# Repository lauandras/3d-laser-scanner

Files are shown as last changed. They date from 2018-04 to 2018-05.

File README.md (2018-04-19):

# 3d-laser-scanner
This is our 3D-laser scanner project from Mechatronics project subject.

Downloaded MatLab packages:
  1) MATLAB Support Package for Arduino Hardware
  2) MATLAB Support Package for USB Webcams
  3) Computer Vision System Toolbox
  4) a
  5) a

Exercise - Feladat (HU)
1 mm alatti felbontással bíró lézer szkenner tervezése, amely alkalmas legalább 300x300x500 mm-es tárgyak külső felületének letapogatására.
Szakirodalom kutatás: Tekintsék át a 3D-s szkennelési eljárásokat, különös tekintettel a Lézeres letapogatásra.
Fejlesztés: Végezzék el a lézeres 3D-s szkenner tervezését és kivitelezését, két webkamera és egy vonallézer felhasználásával. A szerkezet legyen alkalmas a szerkezet együttes szállítására, tárolására és szabványos fényképezőállványra való rögzítésre. 
Tervezzenek (a másik 3D szkenneres csoporttal együttműködve) forgatóasztalt kisméretű (max. 500x500x500 mm) tárgyak 360°-os letapogatásához, amely alkalmas a kamerákkal való szinkronizált mozgatásra.

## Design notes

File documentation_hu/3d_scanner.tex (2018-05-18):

\documentclass[12pt,a4paper]{article}
\usepackage[utf8]{inputenc}
\usepackage{pdfpages}
\usepackage[magyar]{babel}
\usepackage{hyperref}	
\hypersetup{					
colorlinks=false,						
pdfborder={0 0 0},
}
\usepackage{fancyhdr}
\usepackage[left=2cm,right=2cm,top=3.5cm,bottom=3cm,headsep=50pt]{geometry}

%=================================================
% code snippset settings
%=================================================
\usepackage{listings}
\usepackage{color}

\usepackage[framed,numbered]{matlab-prettifier}

\definecolor{dkgreen}{rgb}{0,0.6,0}
\definecolor{gray}{rgb}{0.5,0.5,0.5}
\definecolor{mauve}{rgb}{0.58,0,0.82}
\definecolor{mygreen}{RGB}{28,172,0} % color values Red, Green, Blue
\definecolor{mylilas}{RGB}{170,55,241}

\lstset{language=Matlab,%
	%basicstyle=\color{red},
	breaklines=true,%
	morekeywords={matlab2tikz},
	keywordstyle=\color{blue},%
	morekeywords=[2]{1}, keywordstyle=[2]{\color{black}},
	identifierstyle=\color{black},%
	stringstyle=\color{mylilas},
	commentstyle=\color{mygreen},%
	showstringspaces=false,%without this there will be a symbol in the places where there is a space
	numbers=left,%
	numberstyle={\tiny \color{black}},% size of the numbers
	numbersep=9pt, % this defines how far the numbers are from the text
	emph=[1]{for,end,break},emphstyle=[1]\color{red}, %some words to emphasise
	%emph=[2]{word1,word2}, emphstyle=[2]{style},    
}

\begin{document}
%=================================================
\thispagestyle{empty}
\begin{center}
\\
\large{Budapesti Műszaki- és Gazdaságtudományi Egyetem\\
Gépészmérnöki kar}\\[1cm]
\begin{Huge}
\textbf{Mechatronika projekt}
\end{Huge}\\[0.5cm]

\Large{BMEGEFOAMM3}\\[2cm]
\Huge{\bf{3D szkenner}}\\[2.5cm]
\bf{\Large{Tar Dániel\\[5pt]
		Bognár Máté\\
		Varga Roland}}\\[1cm]

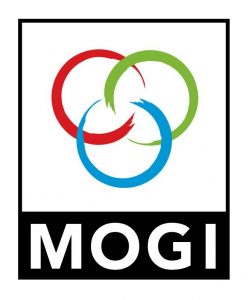
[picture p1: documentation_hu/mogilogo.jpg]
\\[1cm]
\large{\today}
\end{center}
%=================================================
\newpage
\tableofcontents
\newpage
\pagestyle{fancy}
\fancyhf{}
\rhead{Tar Dániel\\Bognár Máté\\Varga Roland}
\lhead{3D szkenner}
\cfoot{\thepage. oldal}
%=================================================
\section{Bevezető} %vargar
Az iparban egyre elterjedtebb a 3D szkennerek alkalmazása. Jól használhatóak gyors prototípuskészítésre és `'reverse engineering'' eljárásokhoz. Ezzel jelentős modellezési és mérési idő takarítható meg.\\[10pt]
Új eszközök tervezésénél és komplex alkatrészek méreteinek gyors meghatározására egyaránt használható. Apróbb mechanikai alkatrészek, turbinalapátok és helységek szkennelése is lehetséges adott felbontással.\\[10pt]
A gyógyászatban alkalmazzák például test vagy testrész modellezésére, mivel egyes protézisek elkészítése nagy méretpontosságot igényel, és így könnyebben formálhatóak az egyéni igények szerint.\\[10pt]
Egyetemeken régészek is használhatják leletek tanulmányozására anélkül, hogy bármilyen kártétel veszélye fennállna.\\[10pt]
\begin{figure}[h!]
\centering
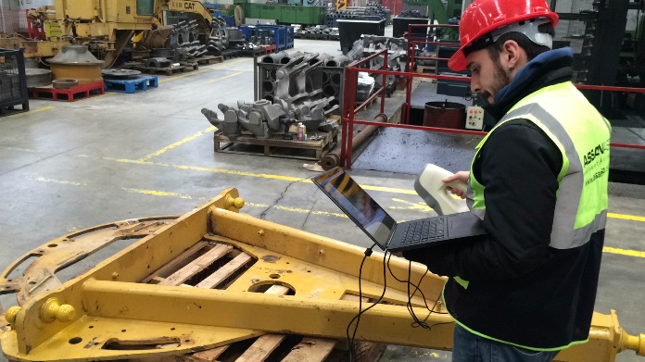
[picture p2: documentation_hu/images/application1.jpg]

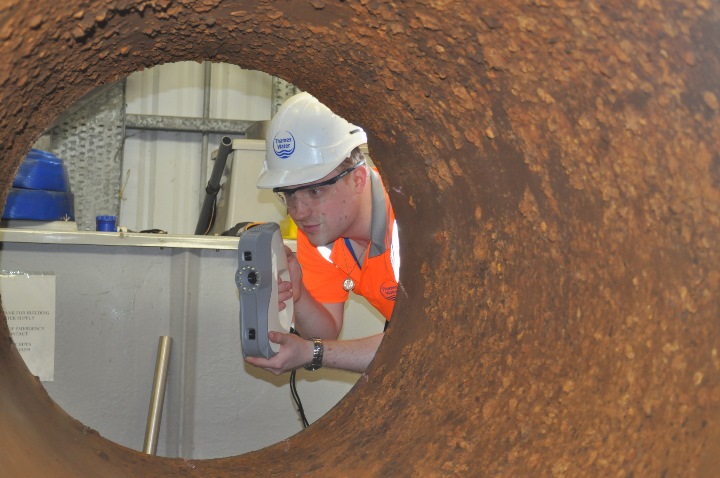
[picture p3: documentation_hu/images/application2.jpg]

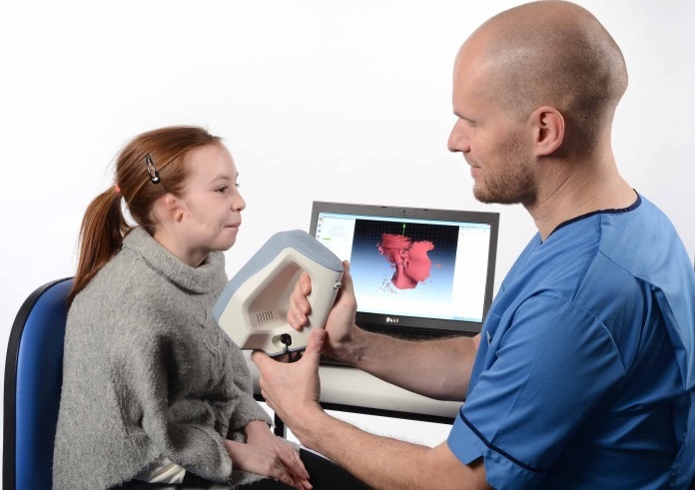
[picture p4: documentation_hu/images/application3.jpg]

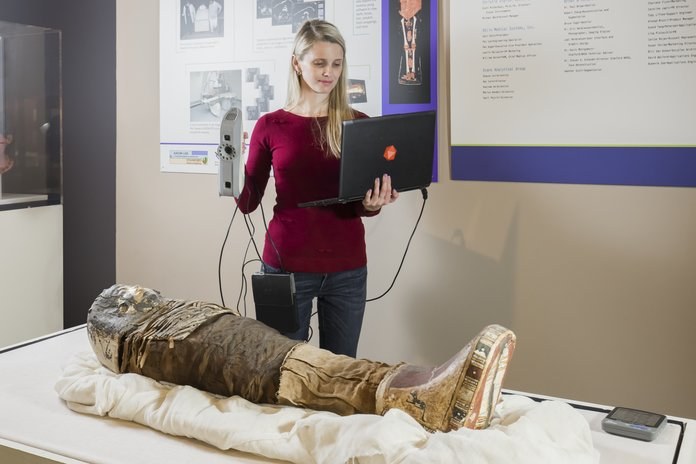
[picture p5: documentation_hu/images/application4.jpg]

\caption{3D szkenner alkalmazása a hétköznapokban\cite{alkalmazasok}}
\end{figure}
%=================================================
\newpage
\section{Feladat leírása} %vargar
\subsection{Követelmények}
A projekt célja egy használható 3D lézerszkenner eljárás kidolgozása és megvalósítása, ami az alábbi követelményeknek megfelel:
\begin{enumerate}
	\item A konstrukció hordozhatósága: viszonylag kis befoglaló mérettel kell 			rendelkezzen és könnyen szétszerelhető-összerakható legyen.\label{hordozhatosag}
	\item A szerkezet legyen alkalmas a szerkezet együttes szabványos fényképezőállványra való rögzítésére.\label{kameraallvanyra}
	\item A megírt program átláthatóságára (felhasználóbarát) és jól dokumentáltságára kell törekedni, hogy a projektet a későbbiekben mások is tovább tudják vinni.\label{felhasznalobarat}
\end{enumerate}
\subsection{Alap koncepció}
A szkennelési módszert egy webkamera, egy vonallézer és egy forgóasztal felhasználásával dolgoztuk ki. Az eljárás lényege, hogy a tárgyra vetült lézerfény vonalról a kamerával valamekkora szögből kép készül. A képen a forgóasztal forgástengelyének meghatározhatónak kell lennie, és ez a vonallézer által meghatározott síkba kell hogy essen. A lézerpontok forgástengelytől (és azon egy tetszőleges origótól) vett távolságából a térbeli helyzetük meghatározható.
%=================================================
\section{Alapul vett szakirodalom} % tard
%=================================================
	%"3d laserscanner" kulcsszót beírva a Google-be rengeteg találatot kap az ember. Mi elsőnek a képi és videó találatokat %nézegettük meg, és rögtön megállapítottuk, hogy nagyon menő lesz az általunk készített kis kütyü / szerkezet.\\
	
	Alapvetően kétféle lézer szkenner található meg a piacon. Az egyik, ami az adott tárgyat, objektumot végigpásztázza egy lézerfény segítségével és a lézerfény kibocsájtásától, a lézerfény visszaérkezéséig eltelt időből számítja a távolságot. Ez egy elég drága technika, mert nagyon pontosan kell mérni az időt. Mivel a fény terjedési sebessége nagyon nagy, ezért körülbelül $[ns]$ nagyságrendben kell mérni az idő múlását.\\[10pt]
	\begin{figure}[h!]
		\begin{center}
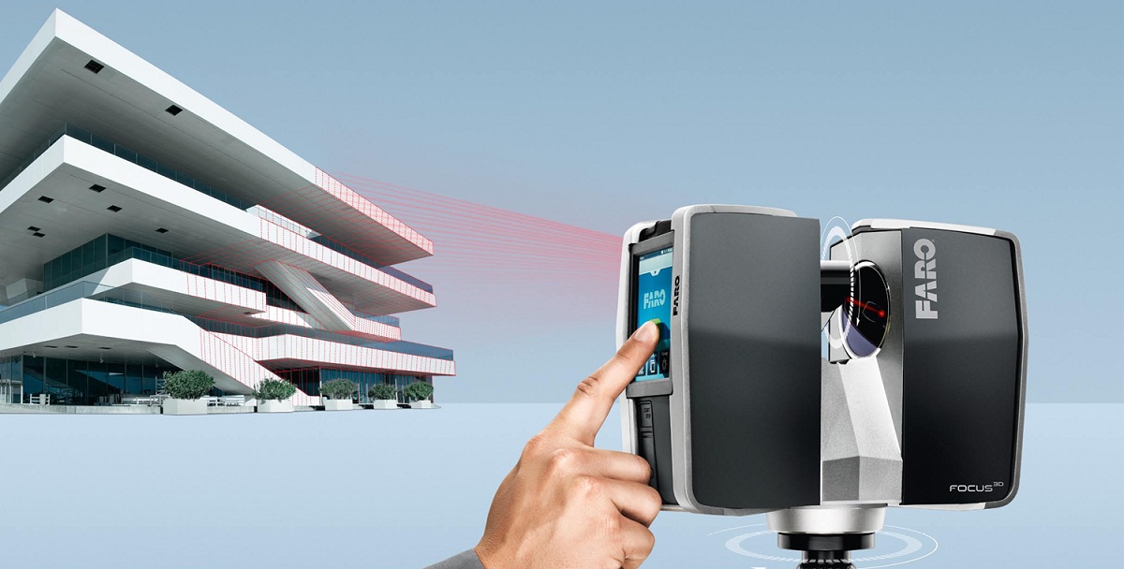
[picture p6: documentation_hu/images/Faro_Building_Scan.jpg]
			
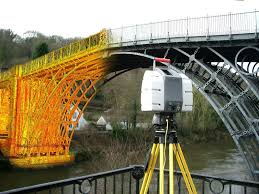
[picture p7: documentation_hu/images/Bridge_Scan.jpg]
			
		\end{center}
		\caption{Távolságmérésen alapuló lézerszkenner\cite{FaroBuildingScan}\cite{BridgeScan}}
	\end{figure}
	A másik, ami egy vonallézerrel világítja meg a tárgy felületét, majd képfeldolgozással felismerve a megvilágított élt, különböző módszerek alapján, előállít egy pontfelhőt. A pontfelhőből háromszögeléses technikával pedig elkészít egy felületmodellt.\\[10pt]
	\begin{figure}[h!]
		\begin{center}
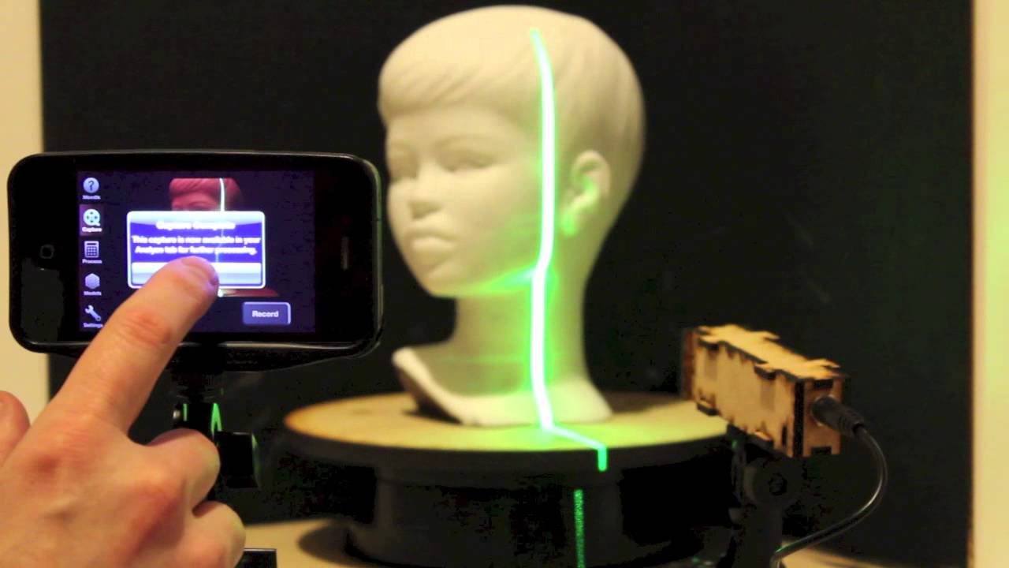
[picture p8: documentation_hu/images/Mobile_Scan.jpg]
			
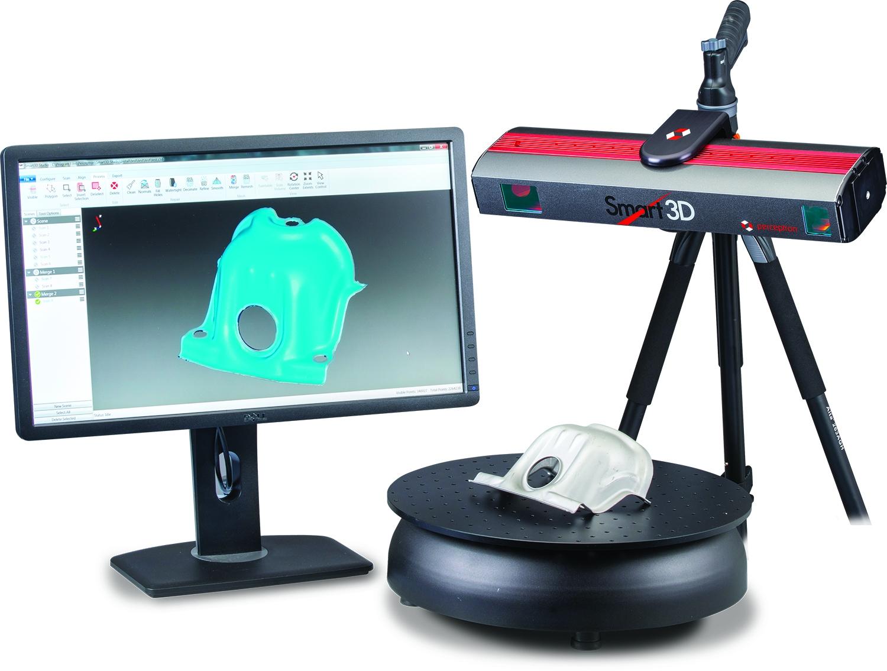
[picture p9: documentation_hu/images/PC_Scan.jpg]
			
		\end{center}
		\caption{Forgóasztalos, képfeldolgozáson alapuló\cite{MobileScan}\cite{PCScan}}
	\end{figure}\\[10pt]
	A rendelkezésre álló eszközök, a feladatleírás és a költségek alapján a második módszert választottuk. A projekt kiindulása képen nagy segítségünkre volt az \href{http://www.instructables.com/id/3D-Laser-Scanning-DIY/}{\textit{Instructables}} oldalon található \textit{DIY: How to Make a Low Cost 3D Scanner}\cite{LaserScannerProjekt} nevű projekt. Ez adott alapot a gondolkodásmódunknak, de végül teljesen más módszerrel dolgozzuk fel az adatokat.

%=================================================
\section{Felhasznált hardverek} % bognarm
%=================================================
\subsection{Beszerzett eszközök}
A projektfeladat már az előző évben is ki volt adva, a tavalyi csoportnak ugyan nem sikerült befejeznie, de néhány általuk készített alkatrész öröklődött. Így már kézhez kaptuk egy  LFL650-5-12(9x20)60-as típusú vonallézert,
egy unipoláris léptető motort, a tanszéki KUTESZ alkatrészekből összeállított állvánnyal és egy kisebb méretű asztallal,
illetve a motor meghajtó áramkört is.
\\[10pt]
A felhasznált hardverek egy másik része Bojtos Attila tanár úrtól származik. Ilyen a fényképezőgép állvány, az erre később rögzített 20x20-as ITEM-5-ös profil, és egy Canyon márkájú, 640x480-as felbontású webkamera.
\\[10pt]
Általunk beszerzett alkatrészek még a következőek: 
\begin{itemize}
	\item 2 db Arduino Nano v3
	\item HC-06 Bluetooh-Serial modul
\end{itemize}
 \begin{figure}[h!]
 	\centering
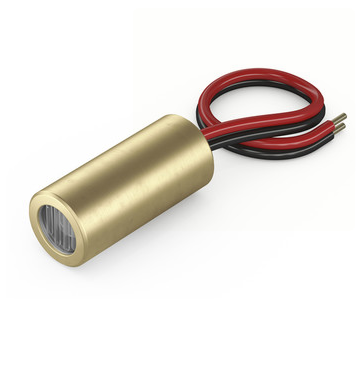
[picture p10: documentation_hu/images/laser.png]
 	
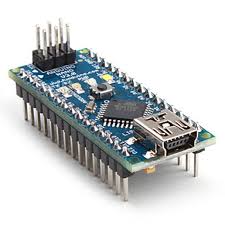
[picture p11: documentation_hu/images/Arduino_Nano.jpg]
 	
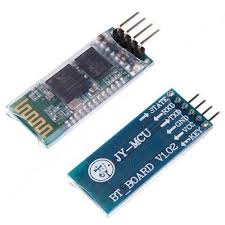
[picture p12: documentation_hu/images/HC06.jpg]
	
	\caption{Beszerzett eszközök}
\end{figure}

\subsection{Saját készítésű eszközök}
Az általunk tervezett alkatrészek többsége 3D nyomtatással készült, ezek a kamerát és lézert az ITEM profilra rögzítő elemek. A lézer lefogó, amely a lézert rögzíti a profil közepén. És a kamera tartó, ami két alkatrész közé szorítja be a kamera alsó részét, a gyári foglalathoz hasonló módon.\\[10pt]
Emellett a követelményeknek megfelelő szkennelhető tárgyméret miatt tervezni kellett egy új forgóasztalt. Ez az asztal 180mm átmérőjű, központosító körökkel ellátott, a KUTESZ elemekkel kompatibilis furatkiosztású elem.
Végül a profilt a kamera állványra rögzítő elem egy 6mm vastag,  lemez alkatrész.
 \begin{figure}[h!]
 	\centering
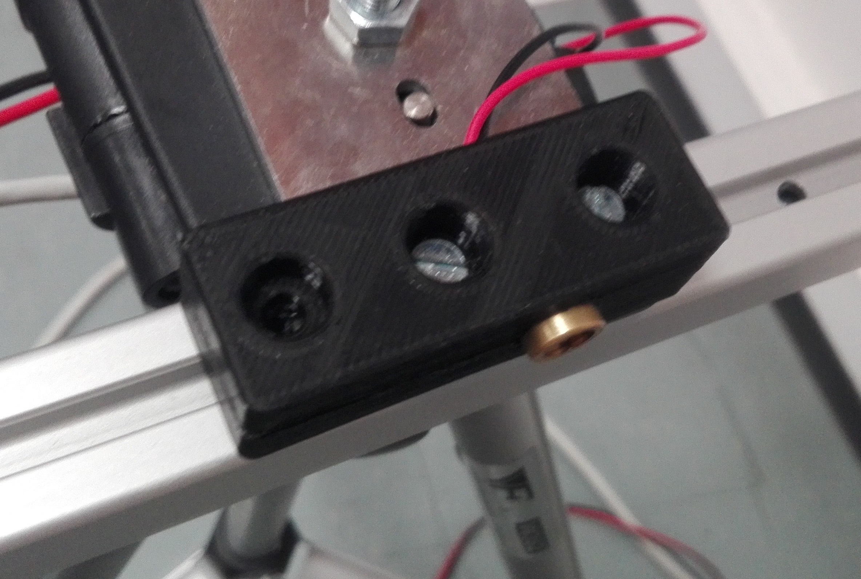
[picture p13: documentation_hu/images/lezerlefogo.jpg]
	
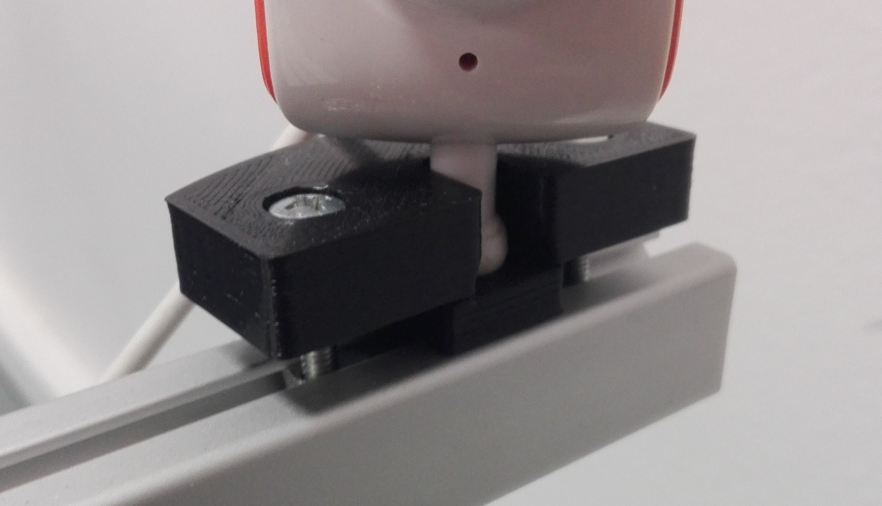
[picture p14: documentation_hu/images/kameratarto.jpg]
	
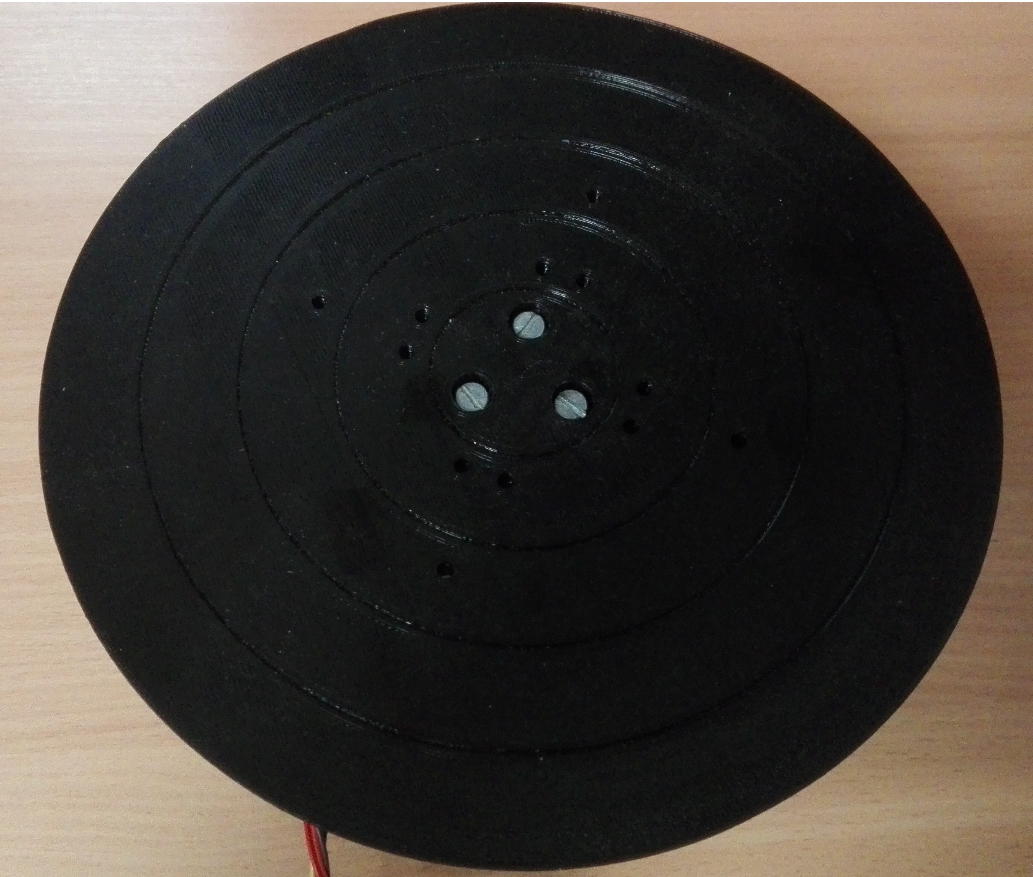
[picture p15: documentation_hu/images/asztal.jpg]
	
	\caption{Saját készítésű eszközök}
\end{figure}\\[10pt]
Készítettünk továbbá még két áramkört, amivel képesek vagyunk Bluetooth-on keresztül vezérelni a forgóasztalt, illetve egy vonallézer vezérlőt, amivel ki-be tudjuk kapcsolgatni a lézert szoftveresen. 

 \begin{figure}[h!]
	\centering
	
	
	\caption{Saját készítésű eszközök}
\end{figure}

\subsection{Hardverek közötti csatlakozás}

Az elkészült konstrukció két részből áll. Az egyik a forgóasztal, a motor, a meghajtója és ennek vezérlő áramköre. A meghajtónak hálózati tápellátás szükséges, míg a vezérlő jelenleg számítógépről kapja az áramot USB-n keresztül.
\\[10pt]
A másik rész a kamera állvány, rajta a lézerrel és webkamerával. Utóbbi közvetlen csatlakozik a számítógéphez, míg a lézer az őt vezérlő arduino-n keresztül, szintén USB segítségével. [\ref{kameraallvanyra}]
\\[10pt]
Így a szkenner két részben hordozható kivitelű. [\ref{hordozhatosag}]
 \begin{figure}[h!]
	\centering
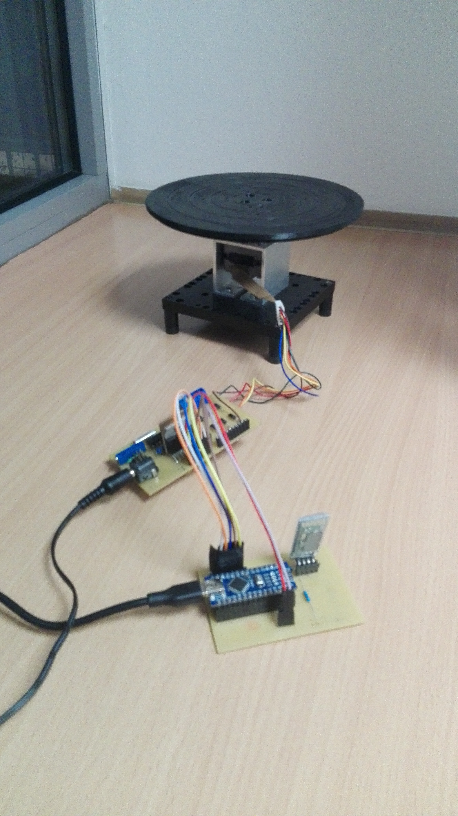
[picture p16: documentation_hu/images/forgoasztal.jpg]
	
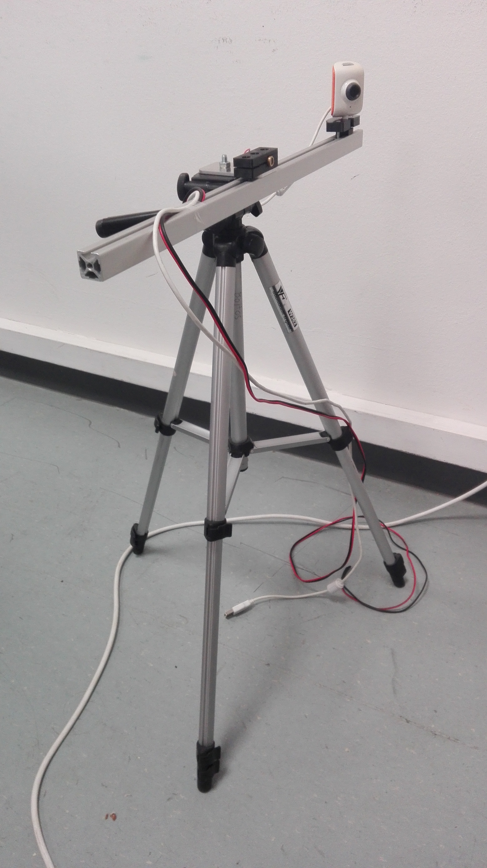
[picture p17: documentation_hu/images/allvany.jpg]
	
	\caption{Saját készítésű eszközök}
\end{figure}
%=================================================
\section{Programkód} %tard
%=================================================
Az egyes szorosan összetartozó részeket külön függvényben írtuk meg, amiket a főprogram, a scan\_object.m hív meg. A függvények csak a továbbiakban is használt változókat adják vissza, így redukáltuk a Workspace-en található vektorok számát. A továbbiakban ezeket fogjuk részletezni elmagyarázni.
%=================================================
\subsection{Kamera kalibráció}
A kamera kalibrációt elsőnek a lézert vezérlő Arduino csatlakoztatásával kezdjük, majd bekapcsoljuk a vonallézert. Ez azért szükséges, hogy a forgóasztal forgástengelyét pontosan a lézer vonalába lehessen helyezni.\\[10pt]
Következő lépésben ellenőrizzük, hogy nincs-e már kalibrálva. Ha igen, akkor ugrunk a következő szekcióra, ha nem akkor pedig megkezdjük a kalibrációs lépéseket:
\begin{enumerate}
	\item Camera Calibrator megnyílása
	\item Képek hozzáadása
	\begin{figure}[h!]
		\centering
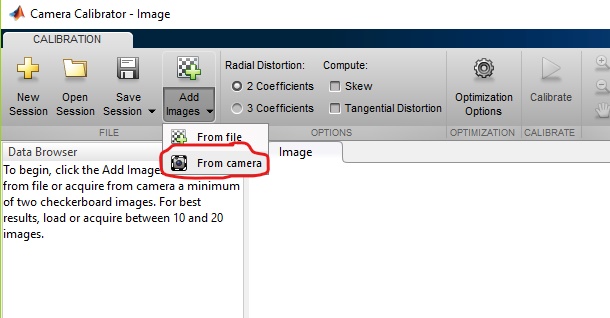
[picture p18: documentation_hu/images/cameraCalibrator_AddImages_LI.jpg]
		
		\caption{Camera Calibrator-ban a képek hozzáadása}
	\end{figure}
	\item A Camera fülön a kameránk kiválasztása
	\item Képek mentési helyének kiválasztása
	\item A képkészítések idejének beállítása
	\item A készítendő képek számának megadása
	\begin{figure}[h!]
		\centering
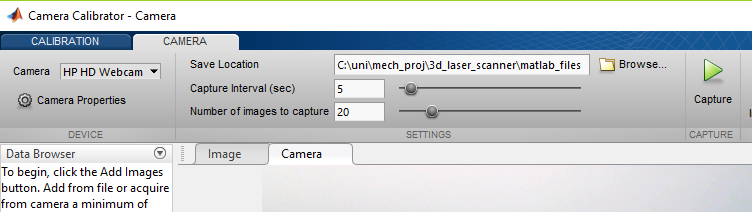
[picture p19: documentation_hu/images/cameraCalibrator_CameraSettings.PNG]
		
		\caption{Képkészítési beállítások megadása}
	\end{figure}
	\item Ha mindent jól beállítottunk, a Capture gombra kattintás 
\end{enumerate}
A sakktáblát célszerű különböző távolságokra, különböző szögekben tartani a kamerához képest, mert akkor pontosabban tud dolgozni az algoritmus. Ajánlott legalább 10-15 kép elkészítése, mielőtt eljutnánk a kalibrációnk kritikus, legnagyobb precizitást igénylő pontjához, a forgástengely beállításához.\\[10pt]
Most úgy kell még 3 képet készíteni, hogy a sakktábla egyik határolóvonala a forgástengellyel egybe essen, merőleges legyen a forgóasztalra és párhuzamos legyen a vonallézernyalábbal. Attól függően, hogy ezt a lépést milyen pontosan végezzük el, befolyásoljuk a beszkennelt 3d-modellünk pontosságát.\\[10pt]
A képek elkészülése utáni felugró ablakban meg kell adni a sakktáblánk egy elemének a méreteit.\\[10pt]
\begin{figure}[h!]
	\centering
	
	\caption{Sakktábla rácsméretének a megadása}
\end{figure}\\[10pt]
A \textit{Calibration} fülön az \textit{Optimization Options}-re, a \textit{Calibrate}, majd az \textit{Export Camera Parameters}-re kattintva ebben a sorrendben, már csak egy lépés marad a kalibrációs folyamatból: Matlab \textit{Command Window}-jában megadni annak a képnek a számát, amelyiken a sakktáblánk párhuzamos volt a lézernyalábbal. A kalibráció során a \textit{Matlab} algoritmusa meghatározza a mintán a négyzetek sarokpontjait, amikhez később, a 5.4-es pontban szükségünk lesz a képtranszformáció meghatározásában.

\begin{figure}[h!]
	\centering
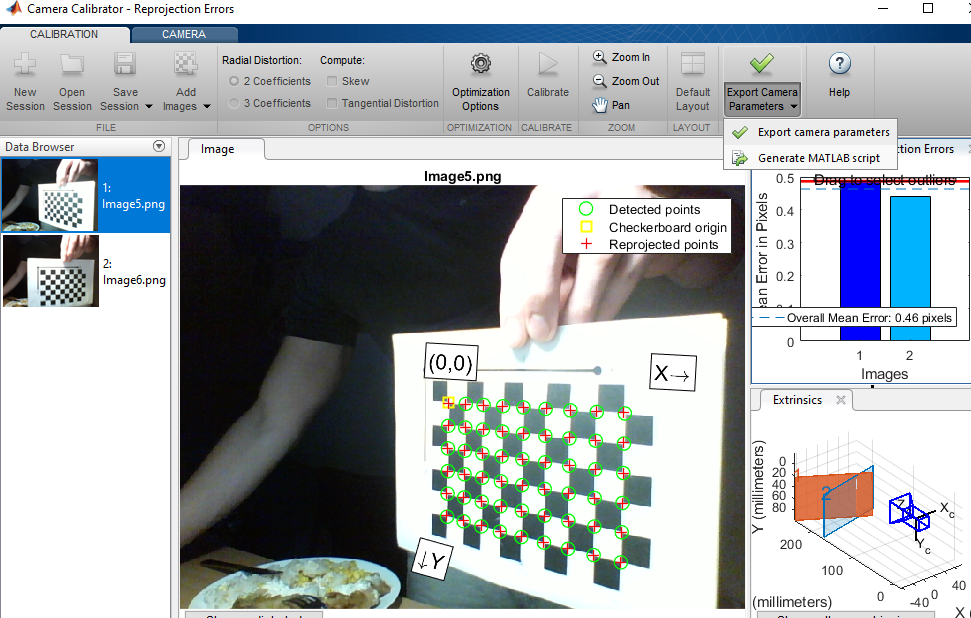
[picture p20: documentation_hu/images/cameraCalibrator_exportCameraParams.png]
	
	\caption{A kalibráció utólsó lépései}
\end{figure}

\begin{figure}[h!]
\centering
\begin{lstlisting}[
style = Matlab-editor,
basicstyle=\tiny
]
%----------------------------------------------------
%   Camera calibration
%----------------------------------------------------

% laserPin - the pin, on which the linelaser is soldered to
laserPin = 'D2';
prompt = 'On which Port is the laser controlling Arduino is connected: ';
laserCom = input(prompt,'s');

% connecting to the laser controlling Arduino on Port 'laserCom'
laserDino = arduino(laserCom,'Nano3');
disp('Laser connected')

% switch on the laser, that you can place the table so, that the laserline
% intersect the rotation axis
writeDigitalPin(laserDino,laserPin,1);

% if 'cameraParams' variable exists, then the calibration process is already done 
if (exist('cameraParams','var')~=1)
% if not then clear the variables for webCam - 'cam', the camera
% calibration toolbox will use it
clear cam

disp('Make minimum 15 pictures, then more 3 so,'+... 
+'that the chessboard pattern is parallel with the laserline!')

% starting camera calibration toolbox
cameraCalibrator
prompt = 'What is the number of the picture, on '+...
+'what the laserline is parallel with the chessboard: ';
paralellImageNumber = input(prompt);
end
\end{lstlisting}
\caption{Kamera kalibrációs rész kódja a scan\_object.m szkriptből}
\end{figure}

%=================================================
\subsection{Perifériák inicializálása}
Ellenőrizzük, hogy az adott perifériák léteznek-e a 'workspace'-n, ha bármelyik hiányzik, akkor kitöröljük mindet, majd újrainicializálunk az \textit{init()} függvény segítségével.
\begin{figure}[h!]
\centering
\begin{lstlisting}[
style = Matlab-editor,
basicstyle=\tiny
]
%----------------------------------------------------
%   Initialization
%----------------------------------------------------

% if there are no camera or laser or turntable variables
% on the workspace

% exist name -- returns 1 if 'name' is a variable in the workspace and 0 if
% not
if ((exist('a','var')&&exist('laserDino','var')&&exist('cam','var'))~=1)
clear a
clear cam
clear laserDino
[a,laserDino,cam]=init(laserCom);
end
\end{lstlisting}
\caption{Az eszközök inicializáló kódja a scan\_object.m szkriptből}
\end{figure}
	
\begin{figure}
\centering
\lstinputlisting[
style = Matlab-editor,
basicstyle=\tiny
]{../matlab_files/init.m}
\caption{Az init() függvény}
\end{figure}

%=================================================
\subsection{Képek vágása}
A szkennelt test felületén lévő piros lézercsík felismerésének, illetve az összes számolás gyorsításához a felhasználó kijelölheti a tárgyat befoglaló területét, majd egy jobb klikkes menüből levághatja a felesleges részeket.
\begin{figure}[h!]
	\centering
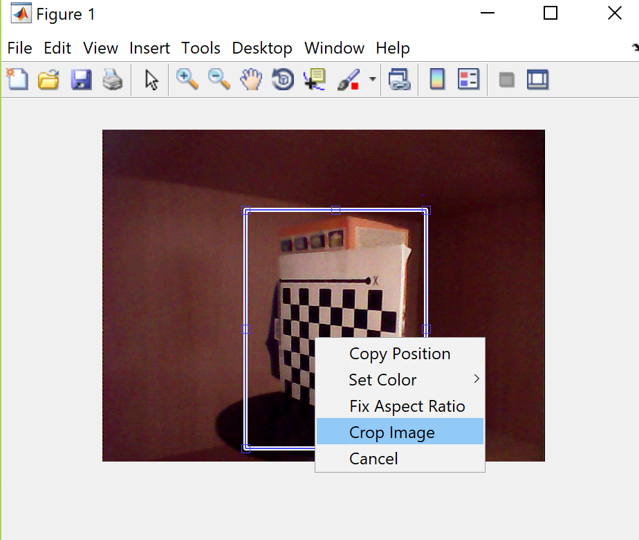
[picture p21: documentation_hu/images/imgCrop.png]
	
	\caption{Képek crop-polása}
\end{figure}\\[10pt]
\begin{figure}[h!]
	\centering
\begin{lstlisting}[
style = Matlab-editor,
basicstyle=\tiny
]
%--------------------------------------------------------
%   Cropping the valuable areas of the images
%--------------------------------------------------------

disp('Place the object on the turntable and then click the figure!')
% show figure window
figure;
% waiting for the click
waitforbuttonpress;
disp('Select the object on the image, then right click and "Crop Image"!')
% take a snapshot and display it on the figure
img=snapshot(cam);
[imgCropped,rect]=imcrop(img);
\end{lstlisting}
	\caption{A kép vágó kód a scan\_object.m szkriptből}
\end{figure}

%=================================================
\subsection{Transzformáció meghatározása}
Azért van szükségünk erre a módszerre, mivel a kameránk elég éles szögben van rögzítve a vonallézerrel, és ez a lézerre párhuzamos sakktáblát perspektívikusan jeleníti meg. Ez nekünk nem jó, mert nagyon sok bonyolult geometriai számítást igénylő programra lenne szükségünk, amivel meghatározható lenne a forgástengely és az adott helyen lévő pont távolsága. A perspektívikus képünket tehát úgy szeretnénk módosítani, hogy a négyszögek négyzetekké alakuljanak, ráadásul akkor négyzetekké, mint a valóságos sakktáblamintánkon.\\[10pt]
Amennyiben ismert 4-4 különböző pont a síkon és a transzformáció jellege (esetünkben: \textit{projektív} - a pontokat összekötő egyenesek egyenesek maradnak), akkor a két ponthalmaz között egyértelműen meghatározható a leképzési transzformáció. Ezt valósítja meg az általunk implementált \textit{imageTform()} nevű függvény.\\[10pt]
\begin{figure}[h!]
\centering
\begin{lstlisting}[
style = Matlab-editor,
basicstyle=\tiny
]
%--------------------------------------------------------
%   Determining the image transformation
%--------------------------------------------------------
[tfHeight,tfWidth,tform,xdata,ydata]=imageTform(imgCropped,rect,paralellImageNumber,cameraParams);
\end{lstlisting}
\caption{A transzformáció meghatározása a scan\_object.m szkriptből}
\end{figure}
A függvény a levágott kép, a vágási határok, a vonallézerre párhuzamos kép ismeretében, és ezen a képen a sakktáblán felismert pontok helyéből meghatározza a leképzési transzformációt, és a leendő áttranszformált képek méreteit.
\begin{figure}[h!]
\centering
\lstinputlisting[
style = Matlab-editor,
basicstyle=\tiny
]{../matlab_files/imageTform.m}
\caption{Az imageTform() függvény}
\end{figure}

%=================================================
\subsection{Szükséges változók deklarálása}
A Matlab különböző dimenziójú mátrixokban tárolja az adatokat/változók értékeit és azért, hogy az értékeinket el tudjuk megfelelően tárolni, létre kell hozni és feltölteni valamilyen kezdeti értékekkel ezeket. Később a változók egyes elemeit indexeléssel meg tudjuk változtatni, illetve ki tudjuk nyerni belőlük az adatokat. Ilyen adatszettek például:
\begin{itemize}
	\item A polárkoordinátás pontfelhőnk
	\item A képeket tároló mátrixok
\end{itemize}
Ebben a programkódrészletben definiáljuk továbbá a program futása során nem változó de lényeges konstansokat:
\begin{itemize}
	\item A forgatások számát, ami szükséges az asztal teljes körülfordulásához
	\item A forgósztalt vezérlő Arduino azon lábát, amelyikkel az órajelet adjuk neki
	\item A készített és levágott képek méreteit
\end{itemize}
\begin{figure}[h!]
	\centering
	\begin{lstlisting}[
	style = Matlab-editor,
	basicstyle=\tiny
	]
	%--------------------------------------------------------
	%   Initializing further variables
	%--------------------------------------------------------
	
	% the number of rotatinos with the turntable makes one total rotation 
	% (360 degree)
	rotations=400;
	
	% getting the height and width of the cropped images
	imgSize = size(img);
	imgHeight = imgSize(1);
	imgWidth  = imgSize(2);
	croppedHeight=int16(rect(4));
	croppedWidth=int16(rect(3));
	
	% initializing the polar point set with maximum pointnumber
	%  - we have 400 pictures from a whole rotation and 
	%  - each picture have an tfHeight on which we will iterate through
	%  - each point have a radius and height coordinate
	polarPointSet_mm = zeros([rotations tfHeight 2]);
	
	% initializing the arrays, what are containing all off the images
	filteredImages=zeros(rotations,croppedHeight,croppedWidth);
	transformedImages=zeros(rotations,tfHeight,tfWidth);
	kepek=zeros([rotations croppedHeight croppedWidth]);
	
	% set the clock signal pin on which we are communicating with the turntable
	clk='D6';
	\end{lstlisting}
	\caption{Változók deklarálása, inicializálása kódrészlet a scan\_object.m szkriptből}
\end{figure}

%=================================================
\subsection{Szkennelés folyamata}
A szkennelés egy iterációs lépéssorozat - amit annyiszor hajtunk végre, ahány egységnyi forgatás szükséges a forgóasztal körbefordulásához - , ami a következő alfolyamatokra bontható le:
\begin{enumerate}
	\item Képkészítés és lézerfény felismerés
	\item Forgóasztal léptetés
	\item Képtranszformáció
	\item Pontfelhő generálás
	\item Státuszbár frissítése
\end{enumerate} 
\begin{figure}[h!]
	\centering
	\begin{lstlisting}[
	style = Matlab-editor,
	basicstyle=\tiny
	]
	%--------------------------------------------------------
	%   Scanning
	%--------------------------------------------------------
	
	% create window
	figure;
	% create status bar
	f=waitbar(0,'Initialization','Name','Making images');
	for idr=1:rotations
	% capturing an image and detect the laserline on it
	laserMask=laser_line_detection(rect,laserDino,laserPin,cam);
	kepek(idr,:,:)=laserMask;
	% rotating the table
	rotateTable(a,clk,400/rotations);
	% transforming the img
	tfLaserMask=imtransform(laserMask,tform);
	% generating the polar pointset
	polarPointSet_mm=createPolarPointSet(tfLaserMask,polarPointSet_mm,idr,xdata,ydata);
	% refreshing the status bar
	waitbar(idr/rotations,f,sprintf('%d/%d',idr,rotations));
	end
	close(f)
	\end{lstlisting}
	\caption{Szkennlés kódrészlete a scan\_object.m szkriptből}
\end{figure}

%=================================================
\subsubsection{Képek készítése és lézerfény detektálása}
A lézerfény felismerés úgy történik, hogy készítünk két képet, egyet lézerfénnyel, egyet anélkül, majd levágjuk a felesleges részeket és szürkeárnyalatossá alakítjuk őket. Ezután kivonjuk a kettőt egymásból, és a létrejövő képen egy gaus-os elmosást alkalmazunk. Az utóbbi ahoz szükséges, hogy a képünkön létrejövő kontrasztos vonalakat kicsit összemossuk. A szűrt képen a \textit{DIY: How to Make a Low Cost 3D Scanner} projektben található algorithmus (\textit{detectLaserLineOnImg()} függvény) kis módosításával és hangolásával meghatározzuk a lézervonal pozícióját. Az egész folyamatot a \textit{laser\_line\_detection()} nevű függvény kontrollálja.
\begin{figure}[h!]
	\centering
	\lstinputlisting[
	style = Matlab-editor,
	basicstyle=\tiny
	]{../matlab_files/laser_line_detection.m}
	\caption{A laser\_line\_detection() függvény}
\end{figure}

%=================================================
\subsubsection{A forgóasztal léptetése}
A tavalyi csapattól örökült H-hidas stepper motor vezérlő áramkör clock lábának pulzálásával lehet az asztalunkat léptetni. A \textit{rotateTable()} függvény amit megalkottunk képes arra, hogy egy hívásra többet is léptesse az asztalt, ez azért praktikus, mert így lehetséges egy gyorsított, habár pontatlanabb szkennelést végezni az objektumon. 
\begin{figure}
\centering
\lstinputlisting[
style = Matlab-editor,
basicstyle=\tiny
]{../matlab_files/rotateTable.m}
\caption{A rotateTable() függvény}
\end{figure}

%=================================================
\subsubsection{Képek transzformációja}
A transzformálást az \textit{imtransform()}, Matlab-ba beépített függvény valósítja meg nekünk, a már korábban meghatározott \textit{tform} transzformációs objektum segítségével.
\begin{figure}[h!]
\centering
\begin{lstlisting}[
style = Matlab-editor,
basicstyle=\tiny
]
% transforming the img
tfLaserMask=imtransform(laserMask,tform);
\end{lstlisting}
\caption{Szkennlés kódrészlete a scan\_object.m szkriptből}
\end{figure}
%=================================================
\subsubsection{Polárkoordinátás Pontfelhő generálása}
Az képtranszformációnk úgy lett kitalálva, hogy 1[mm] távolságra lévő pontokat 1[px]-re képezzünk le és az y és x tengelyekkel párhuzamosak legyenek a sakktábla négyzetei. A 360$^\circ$-os körbeforduláshoz szükséges lépések számából és a lokális koordinátarendszer origójából (a forgástengely és az asztal síkjának metszéspontja) a transzformált képen könnyedén meghatározhatjuk a pontok helyzetét. 
\begin{figure}[h!]
\centering
\lstinputlisting[
style = Matlab-editor,
basicstyle=\tiny
]{../matlab_files/createPolarPointSet.m}
\caption{A createPolarPointSet() függvény}
\end{figure}

%=================================================
\subsection{XYZ pontfelhő számítása}
Utolsó lépésként a polárkoordinátás pontfelhőnket átszámítjuk a \textit{pointCloud()} függvény segítségével és megjelenítjük:
\begin{figure}[h!]
\centering
\begin{lstlisting}[
style = Matlab-editor,
basicstyle=\tiny
]
%--------------------------------------------------------
%   Calculate the pointcloud to xyz coordinatesystem
%--------------------------------------------------------
xyz=pointCloud(rotations,polarPointSet_mm,tfHeight);
pcshow(xyz)
\end{lstlisting}
\caption{A végleges pontfelhő kiszámítása a scan\_object.m szkriptből}
\end{figure}
\begin{figure}[h!]
	\centering
	\lstinputlisting[
	style = Matlab-editor,
	basicstyle=\tiny
	]{../matlab_files/pointCloud.m}
	\caption{Az pointCloud() függvény}
\end{figure}

%=================================================
\section{Eredmények, a módszer korlátai} %tard
A szkennelési pontosságunk - a projekt jelenlegi állása szerint még csak sötétben - 1-2 [mm] közzé esik, ami az általunk használt 640x480-as webkamera felbontássál jónak számít. A mérési pontatlanság mértékét a kalibrációnál fellépő hibák okozzák, amit további alkatrészek készítésével csökkenteni lehetne.\\[10pt]
Felléphető kalibrációs hibák:
\begin{itemize}
	\item Az asztal forgástengelye nem esik teljesen egybe a vonallézerrel
	\item A vonallézer és az asztal lapja nem merőlegesek egymásra
	\item A sakktábla
	\subitem - középső függőleges egyenese nem esett egybe pontosan a forgástengellyel
	\subitem - nem volt párhuzamos a vonalézér síkjával
	\subitem - négyzetrácsmérete nem állanó:
	\subsubitem + a nyomtatási hibák miatt
	\subsubitem + a kinyomtatott lap elhajlása miatt
\end{itemize}
A hibák nagy részét csökkenteni lehetne az asztallap újratervezésével, és rá illeszkedő merőleges sakktáblatartó keret készítésével és a vonallézert tartó állványra plusz vízmértékek felszerelésével.\\[10pt]
Ha az objektumnak matt felülete van és a szkennelést sötétben végezzük el, akkor 1[mm] pontosság alatti pontfelhőt is képes előállítani a programunk pontos kalibráció esetén.\\[10pt]
\begin{figure}[h!]
	\begin{center}
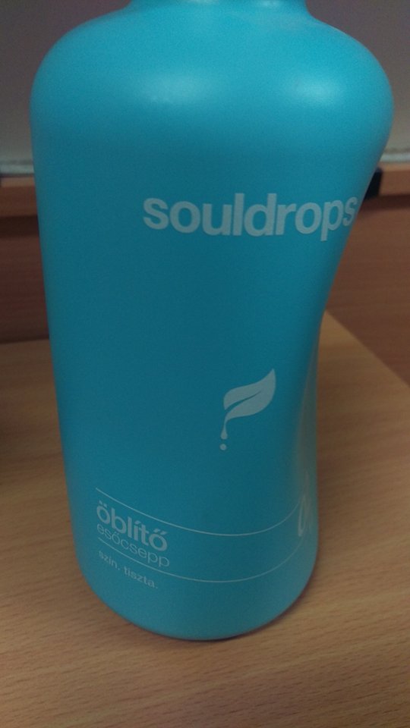
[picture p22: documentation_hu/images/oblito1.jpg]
		
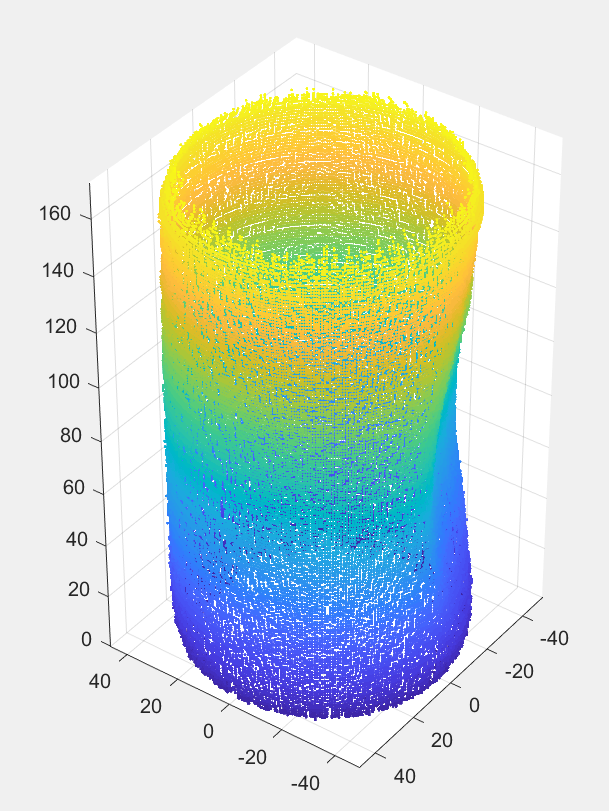
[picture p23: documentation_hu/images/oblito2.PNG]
		
	\end{center}
	\caption{Öblitő palack és 3D-szkennelt pontfelhő}
\end{figure}
Amennyiben a tárgyunknak fényes felülete van, akkor a lézernyaláb megvastagodik, meghízik vagy egyátalán nem látszik a készített képen. A kamera lecserélésével, illetve az ilyen esetekben alkalmazott paraméterhangolással lehetne javítani.\\[10pt]
\begin{figure}[h!]
	\begin{center}
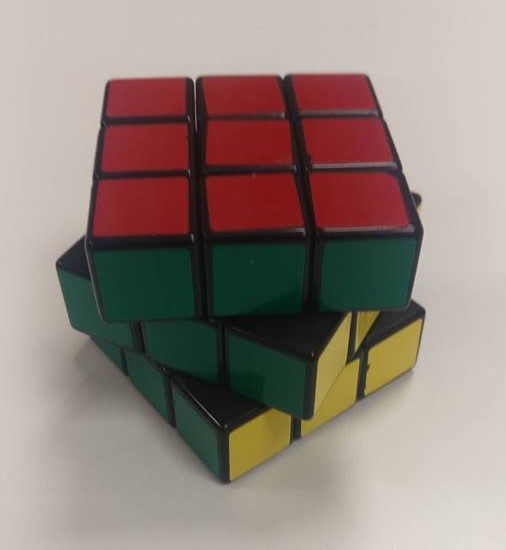
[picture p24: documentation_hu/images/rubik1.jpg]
		
		
		\\
		
		
	\end{center}
	\caption{Rubikkocka és 3D-szkennelt pontfelhő domborodása}
\end{figure}
\begin{figure}[h!]
	\begin{center}
		
		
	\end{center}
	\caption{Az egér és a nem látszó lézerfény miatt keletkezett folt a pontfelhőn}
\end{figure}
A kritikus pontja az eredményeinknek a szkennelési idő, ami jelenleg 20-25 percet vesz igénybe. Az idő redukálására már kidolgozásra került egy módszer, csak implementálása a sok változtás miatt még nem került megvalósításra.\\[10pt]

%=================================================
\section{Továbbfejlesztési irányok} % bognarm
\subsection{Működésbeli}
Ami az eredeti tervhez képest az idő és eszköz hiány miatt nem valósult meg, egy második kamera beszerzése. Ezt a kamerát a lézer másik oldalára rögzítve, a két kamerát egyszerre működtetve a kitakarásokat lehetne csökkenteni, így bonyolultabb geometriájú tárgyak is szkennelhetőek lennének.
\\[10pt]
A szkennelést leginkább lassító tényező a kamera alkalmazkodási ideje a fényerőhöz, a lézeres és lézer nélküli képek között. A megoldás a tárgy kétszeri körbeforgatása lenne, egyszer lézerrel, majd anélkül. A képeket csak ezután dolgozná fel a program. Így az alkalmazkodási időt nem képenként, hanem csak egyszer kellene kivárni, a szkennelés idejét drasztikusan csökkentve.
\subsection{Hardveres}
A hardveres fejlesztések fő célja a szkenner kompaktabbá tétele, működtetésének egyszerűsítése, szállíthatóságának könnyítése.
\\[10pt]
Elsőként a motor meghajtó áramkör újra tervezése és a vezérlő áramkörrel való egybeépítése lenne célszerű. Ezt egyetlen tápcsatlakozóval ellátni, így a forgóasztalnak nem lenne szüksége összeköttetésre a számítógéppel.
Ezután egy ház tervezése és gyártása volna jó, a motor állványa helyett. Ebben rögzíthető lenne a motor mellett az elektronika, egyetlen tápkábel kivezetéssel. Továbbá a ház csúszásgátló talpakkal való felszerelésével a kalibráció utáni esetleges véletlenszerű elmozdítások veszélye csökkenne.
\\[10pt]
Egy következő fejlesztés lehetne a kalibráció könnyítése érdekében, a kalibráló mátrix merev lemezre nyomtatása. Ez a lemez, megfelelő méretekkel megalkotva, csapokkal a forgóasztal furataiba illeszkedne úgy, hogy a mátrix pontosan az asztal közepén helyezkedne el, így javítva a kalibrációt.
\\[10pt]
Egyéb fejlesztési lehetőség a lézert működtető, jelenleg rögzítetlen áramkör forrasztása, elhelyezése az állványra.
\\[10pt]
A szkennelést tovább javítaná a mostani piros lézer lecserélése. Egy zöld lézer nem csak nagyobb intenzitású, de színének előfordulása ritkább a környezetben, ezért a tárgyra vetülő képe egyszerűbben érzékelhető a kamera által.
\subsection{Programbeli}
A program elsődleges fejlesztési iránya a kamera kép szűrésének optimalizálása. A lézer vonalának minél tisztább detektálása végett. Jelenleg a szkenner világos környezetben nem, vagy csak alig képes a pontok vissza adására.
\\[10pt]
További fejlesztési irány egy könnyen kezelhető felhasználói felület készítése a programhoz, annak érdekében, hogy ne csak a program működésének ismerői legyenek képesek a használatára.
\\[10pt]
A jelenlegi program kimenete egy pontfelhő. Továbblépésként megvalósítható a ponthalmaz CAD szoftverbe importálása közvetlen, vagy közvetve, felületek illesztésével.
%=================================================
\newpage
\begin{thebibliography}{9} 
	
%=================================================
\bibitem{feladatkiiras} 
Feladatkiírás
\href{http://mogi.bme.hu/letoltes/MECHATRONIKAI%20&%20IR%C3%81NY%C3%8DT%C3%81STECHNIKAI%20T%C3%81RGYAK/MECHATRONIKA_PROJEKT_BMEGEFOAMM3/Feladatlapok_M/}
{[link]}
%=================================================
\bibitem{alkalmazasok} 
3D szkennelés gyakorlati alkalmazása
\href{https://www.artec3d.com/applications}{[link]}
%=================================================
\bibitem{FaroBuildingScan} 
\href{http://lanmarservices.com/wp-content/uploads/2014/04/Faro_Building_Scan.jpg}{Távolságmérésen alapuló lézerszkenner 1}
%=================================================
\bibitem{BridgeScan}
\href{https://i1.wp.com/cmfenews.com/wp-content/uploads/2018/04/3D-Laser.jpg?fit=1600%2C1200&ssl=1}{Távolságmérésen alapuló lézerszkenner 2}
%=================================================
\bibitem{MobileScan} 
\href{https://i.ytimg.com/vi/RVgyyIlQydg/maxresdefault.jpg}{Forgóasztalos, képfeldolgozáson alapuló 1}
%=================================================
\bibitem{PCScan}
\href{https://3dprint.com/wp-content/uploads/2015/03/Fig.-1-New-Perceptron-Smart3D-Laser-Scanning-System-3.jpg}{Forgóasztalos, képfeldolgozáson alapuló 2}
%=================================================
\bibitem{LaserScannerProjekt}
\href{http://www.instructables.com/id/3D-Laser-Scanning-DIY/}{DIY: How to Make a Low Cost 3D Scanner}
%=================================================
\bibitem{ArduinoNano}
\href{https://potentiallabs.com/cart/image/cache/catalog/New%20Components/Nano_1-800x800.jpg}{Arduino Nano}
%=================================================
\bibitem{HC06}
\href{http://www.robotistan.com/hc06-serial-port-bluetooth-module-12526-82-B.jpg}{HC06 Modul}
%=================================================

\end{thebibliography}

\end{document}

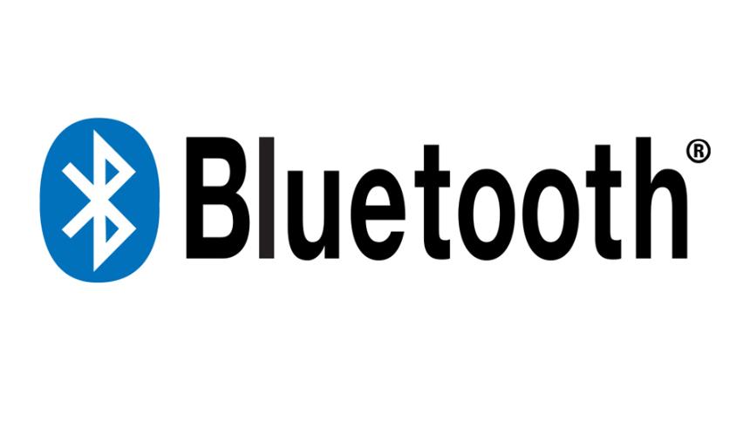
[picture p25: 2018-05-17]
presentation_hu/kepek/image-411064-860_poster_16x9-btgn-411064.jpg

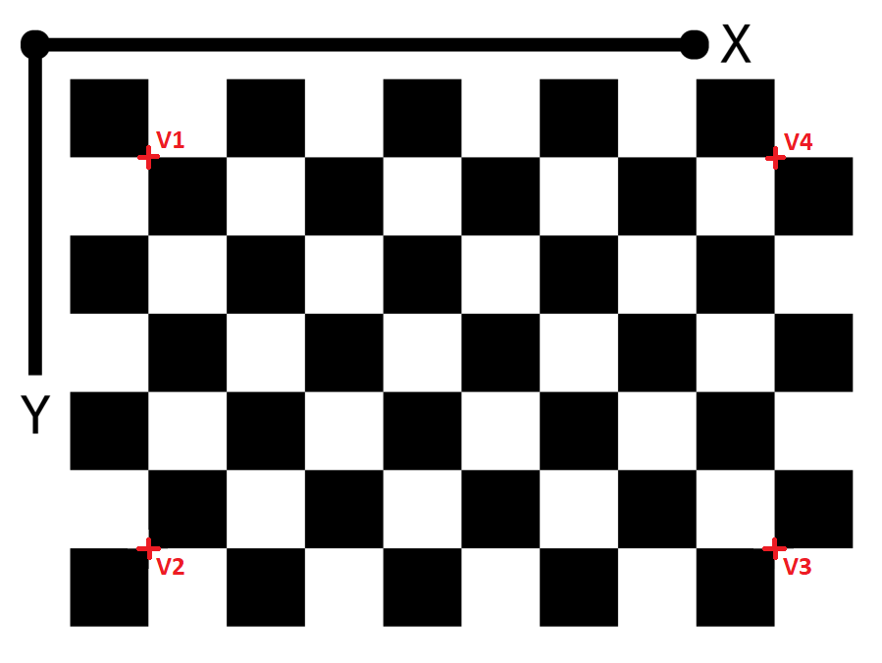
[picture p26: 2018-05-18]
documentation_hu/images/imageTransform.PNG

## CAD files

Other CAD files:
3D_modelled_parts/Kameralefogov3.ipt
3D_modelled_parts/Kameratalpv3.ipt
3D_modelled_parts/Lezerlefogov3.ipt
3D_modelled_parts/asztalv2.ipt

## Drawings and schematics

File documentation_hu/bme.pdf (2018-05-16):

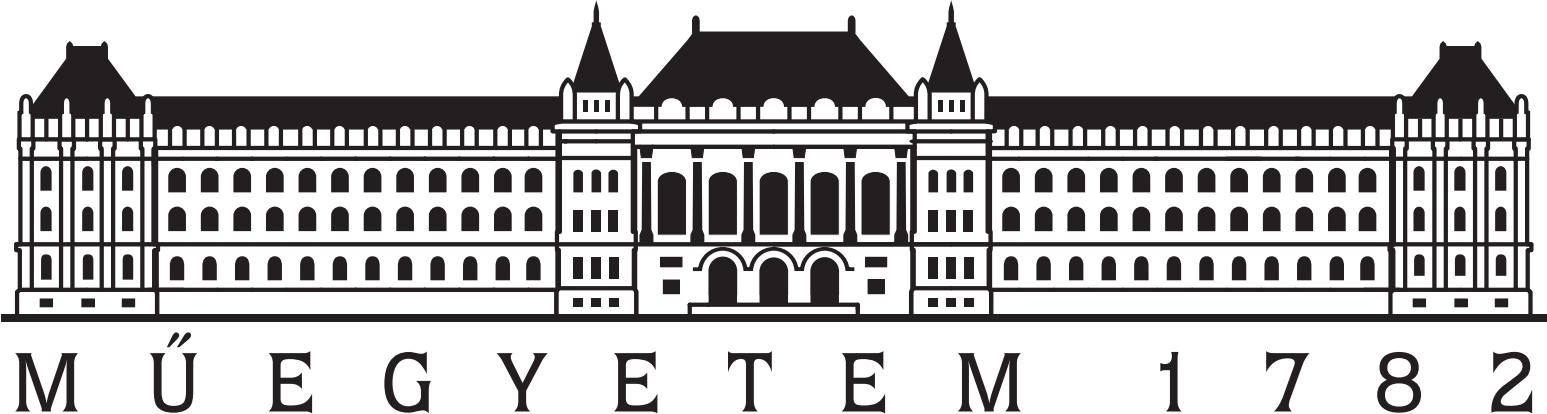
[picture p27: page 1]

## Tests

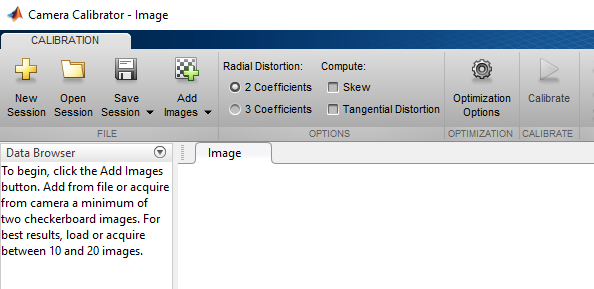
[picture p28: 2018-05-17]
documentation_hu/images/cameraCalibrator.PNG

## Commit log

2018-04-15 camera calibration script added - filterImage script added, but it is not working yet
2018-04-15 new function prototype added - filterLaserLine.m
2018-04-16 functions for laser line detection
2018-05-02 laser line detection bug fixed - but can be improved
2018-05-03 imageCrop function fixed - working with subdirectory calibration_images
2018-05-14 new rotation height calculation - operates only with one filter
2018-05-14 filtered images for toilet paper - not cropped
2018-05-14 filtered images for jbl charge 3 - not cropped
2018-05-14 operates with cropped images and only use one laser line detection method
2018-05-15 Controllers and camera clear in the main program, progressbar fixed
2018-05-16 3D modelled parts added
    [Kameralefogov3.ipt, Kameratalpv3.ipt, Lezerlefogov3.ipt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]
2018-05-16 laser scanning method1 added
2018-05-17 camera calibration part translated to english
2018-05-17 formatting camera calibration part
2018-05-18 fixed y-axis shift
2018-05-18 y-axis shift caused hanges reverted to original
